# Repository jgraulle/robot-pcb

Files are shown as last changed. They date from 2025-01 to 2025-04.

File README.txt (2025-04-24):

Generate file for jlcpcb production:
- Run DRC check
- Generating Gerbers
   - File -> Fabrication Outputs -> Gerbers (.gbr)
   - Select the folder "build"
   - Layer selection, List of layers that should be selected:
      - F.Cu
      - B.Cu
      - F.Paste
      - B.Paste
      - F.Silkscreen
      - B.Silkscreen
      - F.Mask
      - B.Mask
      - Edge.Cuts - (contain the board outline/cutouts.)
   - Jump to General Options and check these:
      - Select Plot reference designators, otherwise designators will not appear on silkscreen layers
      - Select Plot footprint text
      - Select Check zone fills before plotting
      - Select Tent vias
      - Select Use Protel filename extensions, this is recommended as JLCPCB prefers Protel filename extensions
      - Select Subtract soldermask from silkscreen, this ensures no silkscreen on pads
   - Click the Plot button at the bottom of the window
- Generate Drill files
   - From previous window press the "Generate Drill files..." button
   - Check Use alternate drill mode for "Oval Holes Drill Mode"
   - Check Absolute for "Drill Origin"
   - Check Millimeters for "Drill Units"
   - Check Decimal format for "Zeros Format"
   - Click the Generate Drill File button, the drill files will be generated and stored in the output folder
- Generate Drill Map file
   - From previous window press the "Generate Map File" button and everything is going to be done automatically.
- Generate Bill of Materials
   - From Schematic Layout Editor. From the menu bar, click Tool -> Generate Bill of Materials
   - In edit tab, Only check in this order:
      - "Value" with label "Comment"
      - "Reference" with label "Designator"
      - "Package" with label "Footprint"
      - "LCSC" with label "LCSC part number"
   - In export tab:
       Set output file "build/robot-5A-bom.csv"
      - Clic on export
- Generate Pick and Place files
   - From the PCB editor, click on File -> Fabrication output -> Footprint position (.pos) file and export the file with the following settings:
      - CSV
      - mm
      - One file per side
      - Use drilling/placement origin
   - Run the scrip "jlcGenerate.sh"

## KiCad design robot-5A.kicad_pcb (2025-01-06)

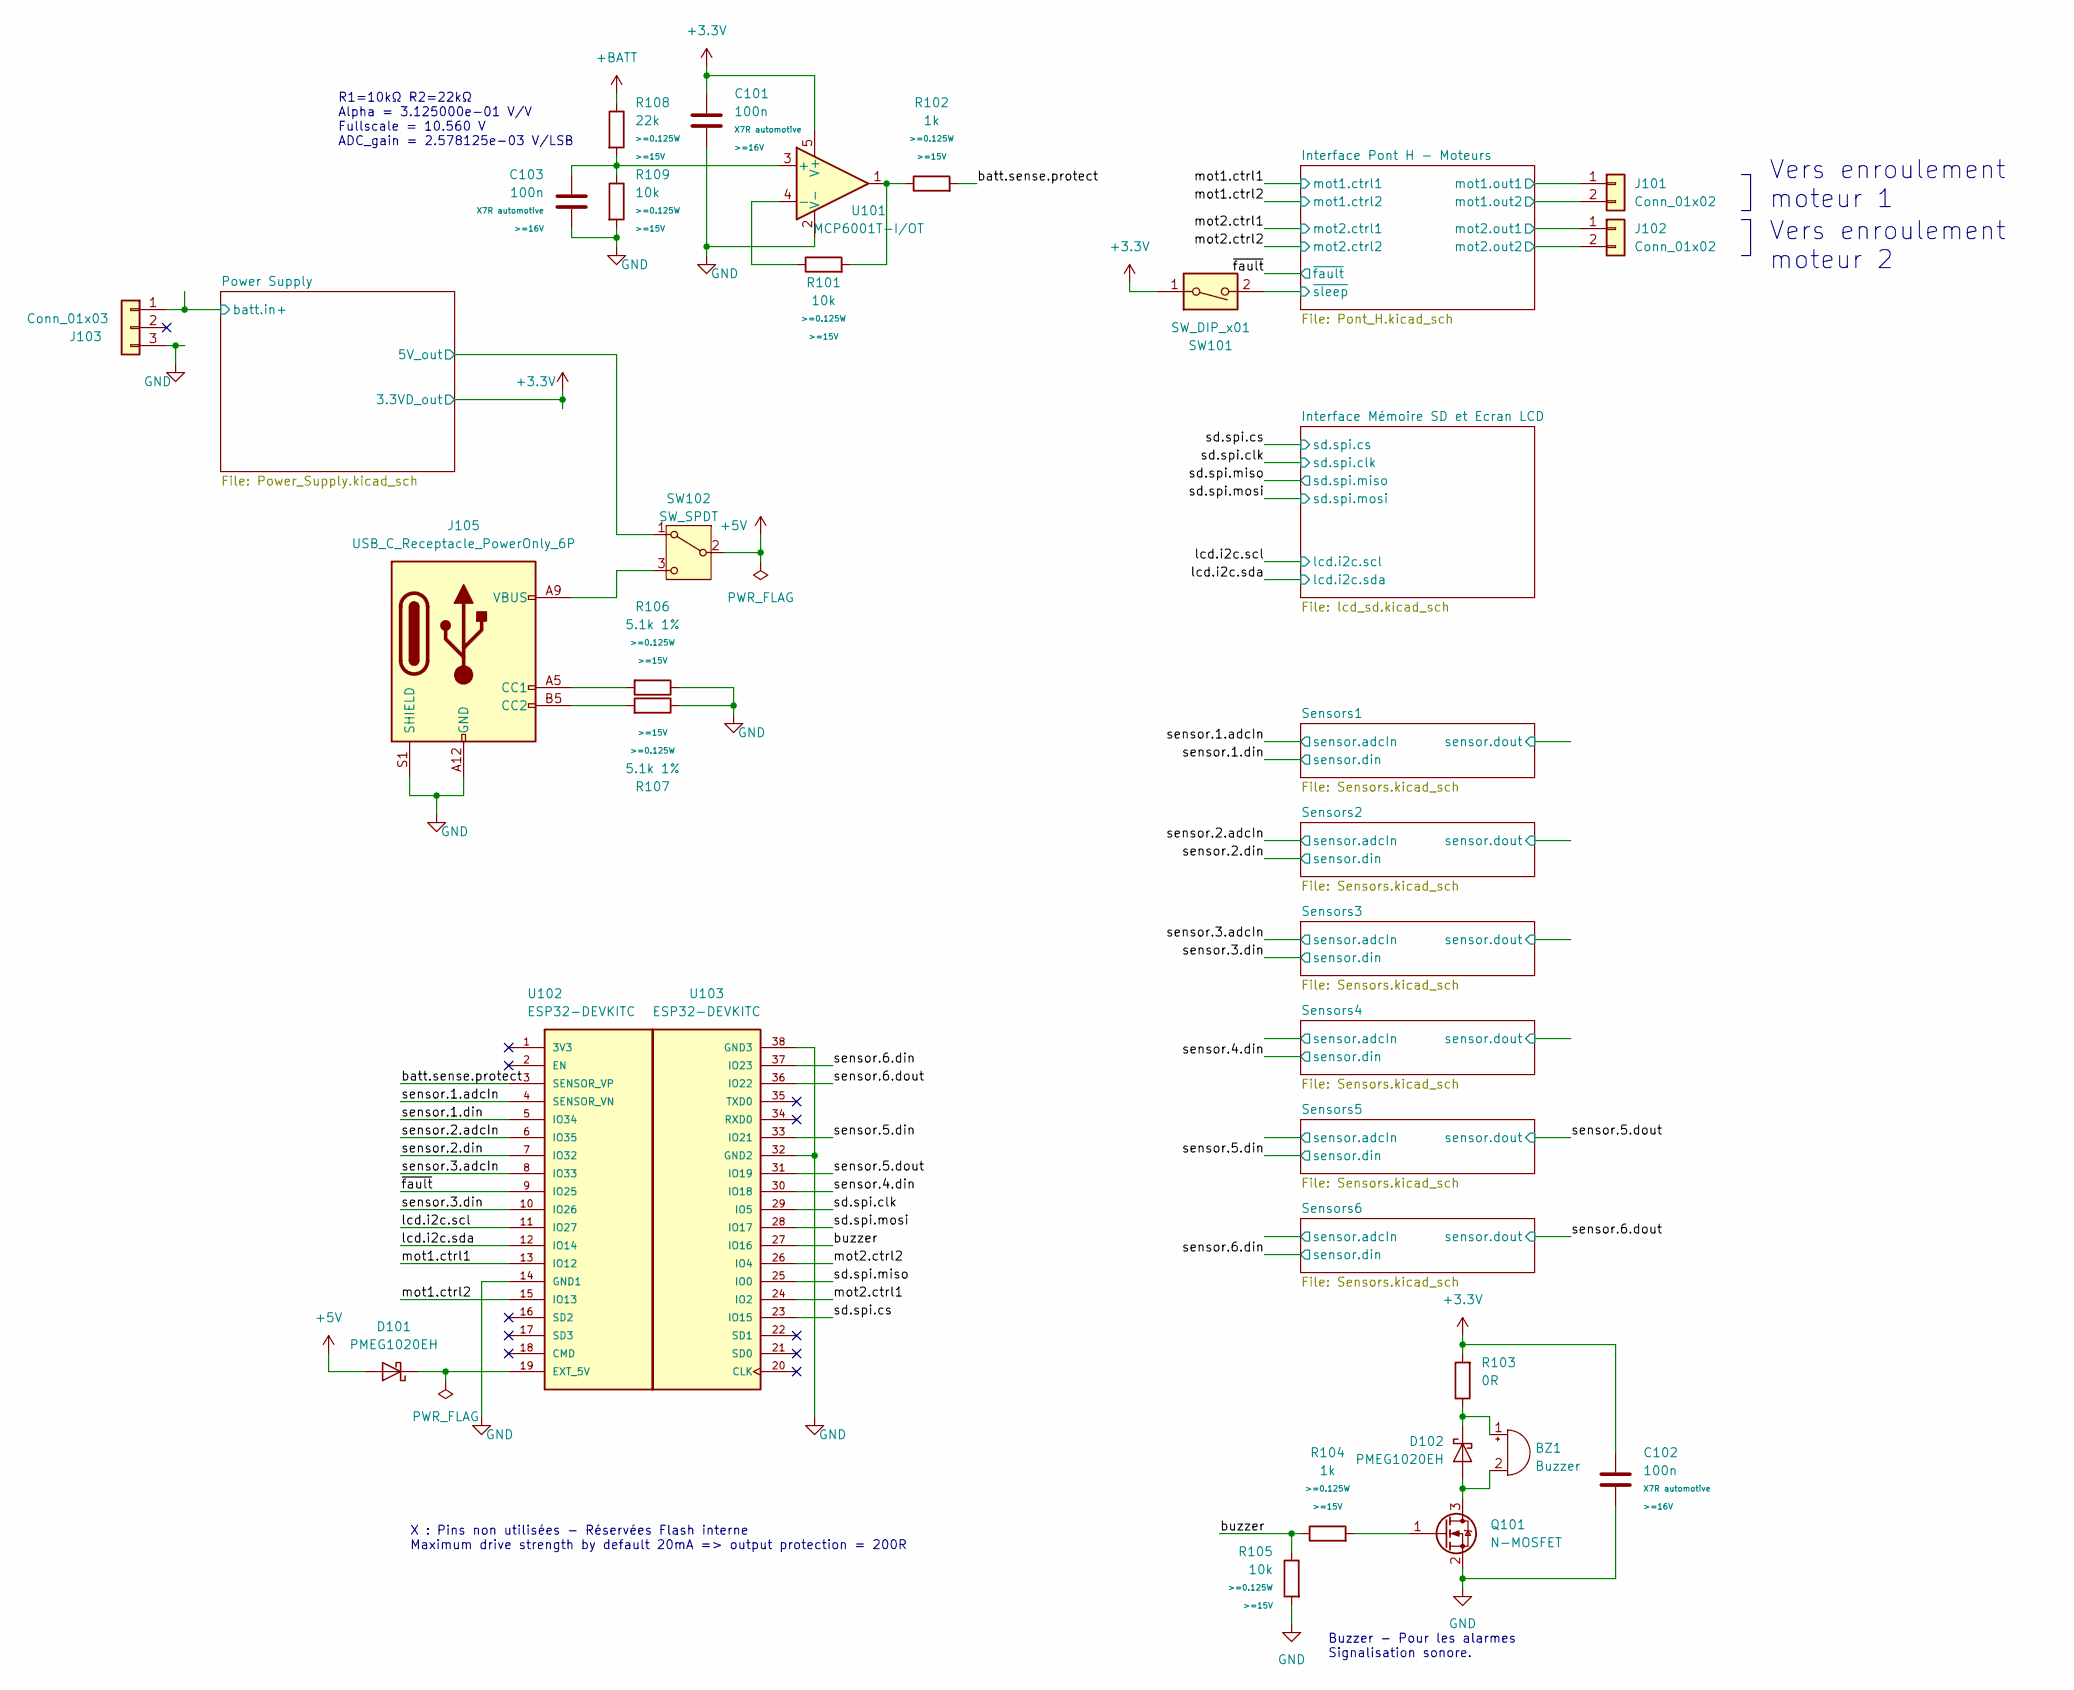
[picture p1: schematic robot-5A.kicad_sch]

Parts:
BZ1: Buzzer; MagneticBuzzer_PUI_AT-0927-TT-6-R; MPN QMB-09B-03; LCSC C96256
C101, C102, C103: 100n; C_0805_2012Metric; Tolerance <=10%; LCSC C28233
D101, D102: PMEG1020EH; D_SOD-123F; MPN PMEG1020EH; LCSC C552798
J101, J102: Conn_01x02; JST_XH_B2B-XH-AM_1x02_P2.50mm_Vertical; MPN XH 2.54; LCSC C158012
J103: Conn_01x03; JST_XH_B3B-XH-AM_1x03_P2.50mm_Vertical; MPN XH 2.54; LCSC C144394
J105: USB_C_Receptacle_PowerOnly_6P; USB_C_Receptacle_SHOU-HAN_TYPE-C-6P-LT-10.5; MPN TYPE-C 6P LT-10.5; LCSC C2681551
Q101: N-MOSFET; SOT-23; MPN AO3414; LCSC C48850
R101, R105, R109: 10k; R_0805_2012Metric; Tolerance <=1%; LCSC C17414
R102, R104: 1k; R_0805_2012Metric; Tolerance <=1%; LCSC C17513
R103: 0R; R_0805_2012Metric; LCSC C844192
R106, R107: 5.1k 1%; R_0805_2012Metric; Tolerance <=1%; LCSC C27834
R108: 22k; R_0805_2012Metric; Tolerance <=1%; LCSC C17560
SW101: SW_DIP_x01; SW_DIP_SPSTx01_Slide_9.78x4.72mm_W7.62mm_P2.54mm; LCSC C126888
SW102: SW_SPDT; SW_Slide_1P2T_SS-12F45; MPN SS-12F45-G040; LCSC C2876011
U101: MCP6001T-I/OT; SOT-23-5; LCSC C116490
U102, U103: ESP32-DEVKITC; MODULE_ESP32-DEVKITC; PARTREV N/A; LCSC C2932678

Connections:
+3.3V: C101.2, C102.2, R103.2, SW101.1, U101.5 (V+); also elsewhere on the board
+5V: D101.2 (A), SW102.2 (B); also elsewhere on the board
+BATT: R108.1; also elsewhere on the board
/Interface Pont H - Moteurs/mot1.out1: J101.1; also elsewhere on the board
/Interface Pont H - Moteurs/mot1.out2: J101.2; also elsewhere on the board
/Interface Pont H - Moteurs/mot2.out1: J102.1; also elsewhere on the board
/Interface Pont H - Moteurs/mot2.out2: J102.2; also elsewhere on the board
/Interface Pont H - Moteurs/~sleep: SW101.2; also elsewhere on the board
/Power Supply/5V_out: SW102.1 (A); also elsewhere on the board
/Power Supply/batt.in+: J103.1; also elsewhere on the board
/batt.sense.protect: R102.2, U102.3 (SENSOR_VP)
/buzzer: R104.1, R105.1, U103.27 (IO16)
/lcd.i2c.scl: U102.11 (IO27); also elsewhere on the board
/lcd.i2c.sda: U102.12 (IO14); also elsewhere on the board
/mot1.ctrl1: U102.13 (IO12); also elsewhere on the board
/mot1.ctrl2: U102.15 (IO13); also elsewhere on the board
/mot2.ctrl1: U103.24 (IO2); also elsewhere on the board
/mot2.ctrl2: U103.26 (IO4); also elsewhere on the board
/sd.spi.clk: U103.29 (IO5); also elsewhere on the board
/sd.spi.cs: U103.23 (IO15); also elsewhere on the board
/sd.spi.miso: U103.25 (IO0); also elsewhere on the board
/sd.spi.mosi: U103.28 (IO17); also elsewhere on the board
/sensor.1.adcIn: U102.4 (SENSOR_VN); also elsewhere on the board
/sensor.1.din: U102.5 (IO34); also elsewhere on the board
/sensor.2.adcIn: U102.6 (IO35); also elsewhere on the board
/sensor.2.din: U102.7 (IO32); also elsewhere on the board
/sensor.3.adcIn: U102.8 (IO33); also elsewhere on the board
/sensor.3.din: U102.10 (IO26); also elsewhere on the board
/sensor.4.din: U103.30 (IO18); also elsewhere on the board
/sensor.5.din: U103.33 (IO21); also elsewhere on the board
/sensor.5.dout: U103.31 (IO19); also elsewhere on the board
/sensor.6.din: U103.37 (IO23); also elsewhere on the board
/sensor.6.dout: U103.36 (IO22); also elsewhere on the board
/~fault: U102.9 (IO25); also elsewhere on the board
GND: C101.1, C102.1, C103.2, J103.3, J105.A12 (GND), J105.B12 (GND), J105.S1 (SHIELD), Q101.2 (S), R105.2, R106.1, R107.1, R109.2, U101.2 (V-), U102.14 (GND1), U103.32 (GND2), U103.38 (GND3); also elsewhere on the board
unnamed 48: D102.2 (A), Q101.3 (D); also elsewhere on the board
unnamed 49: D102.1 (K), R103.1; also elsewhere on the board
unnamed: D101.1 (K), U102.19 (EXT_5V)
unnamed: J105.A5 (CC1), R106.2
unnamed: J105.B5 (CC2), R107.2
unnamed: Q101.1 (G), R104.2
unnamed: R101.2, R102.1, U101.1
unnamed: J105.A9 (VBUS), J105.B9 (VBUS), SW102.3 (C)
unnamed: C103.1, R108.2, R109.1, U101.3 (+)
unnamed: R101.1, U101.4 (-)

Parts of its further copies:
BZ101: Buzzer; MagneticBuzzer_PUI_AT-0927-TT-6-R; MPN QMB-09B-03; LCSC C96256

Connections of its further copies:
unnamed 48: BZ101.2 (+); also elsewhere on the board
unnamed 49: BZ101.1 (-); also elsewhere on the board

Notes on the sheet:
Vers enroulement moteur 1
R1=10kΩ R2=22kΩ Alpha = 3.125000e-01 V/V Fullscale = 10.560 V ADC_gain = 2.578125e-03 V/LSB
X : Pins non utilisées - Réservées Flash interne Maximum drive strength by default 20mA => output protection = 200R
Vers enroulement moteur 2
Buzzer - Pour les alarmes Signalisation sonore.

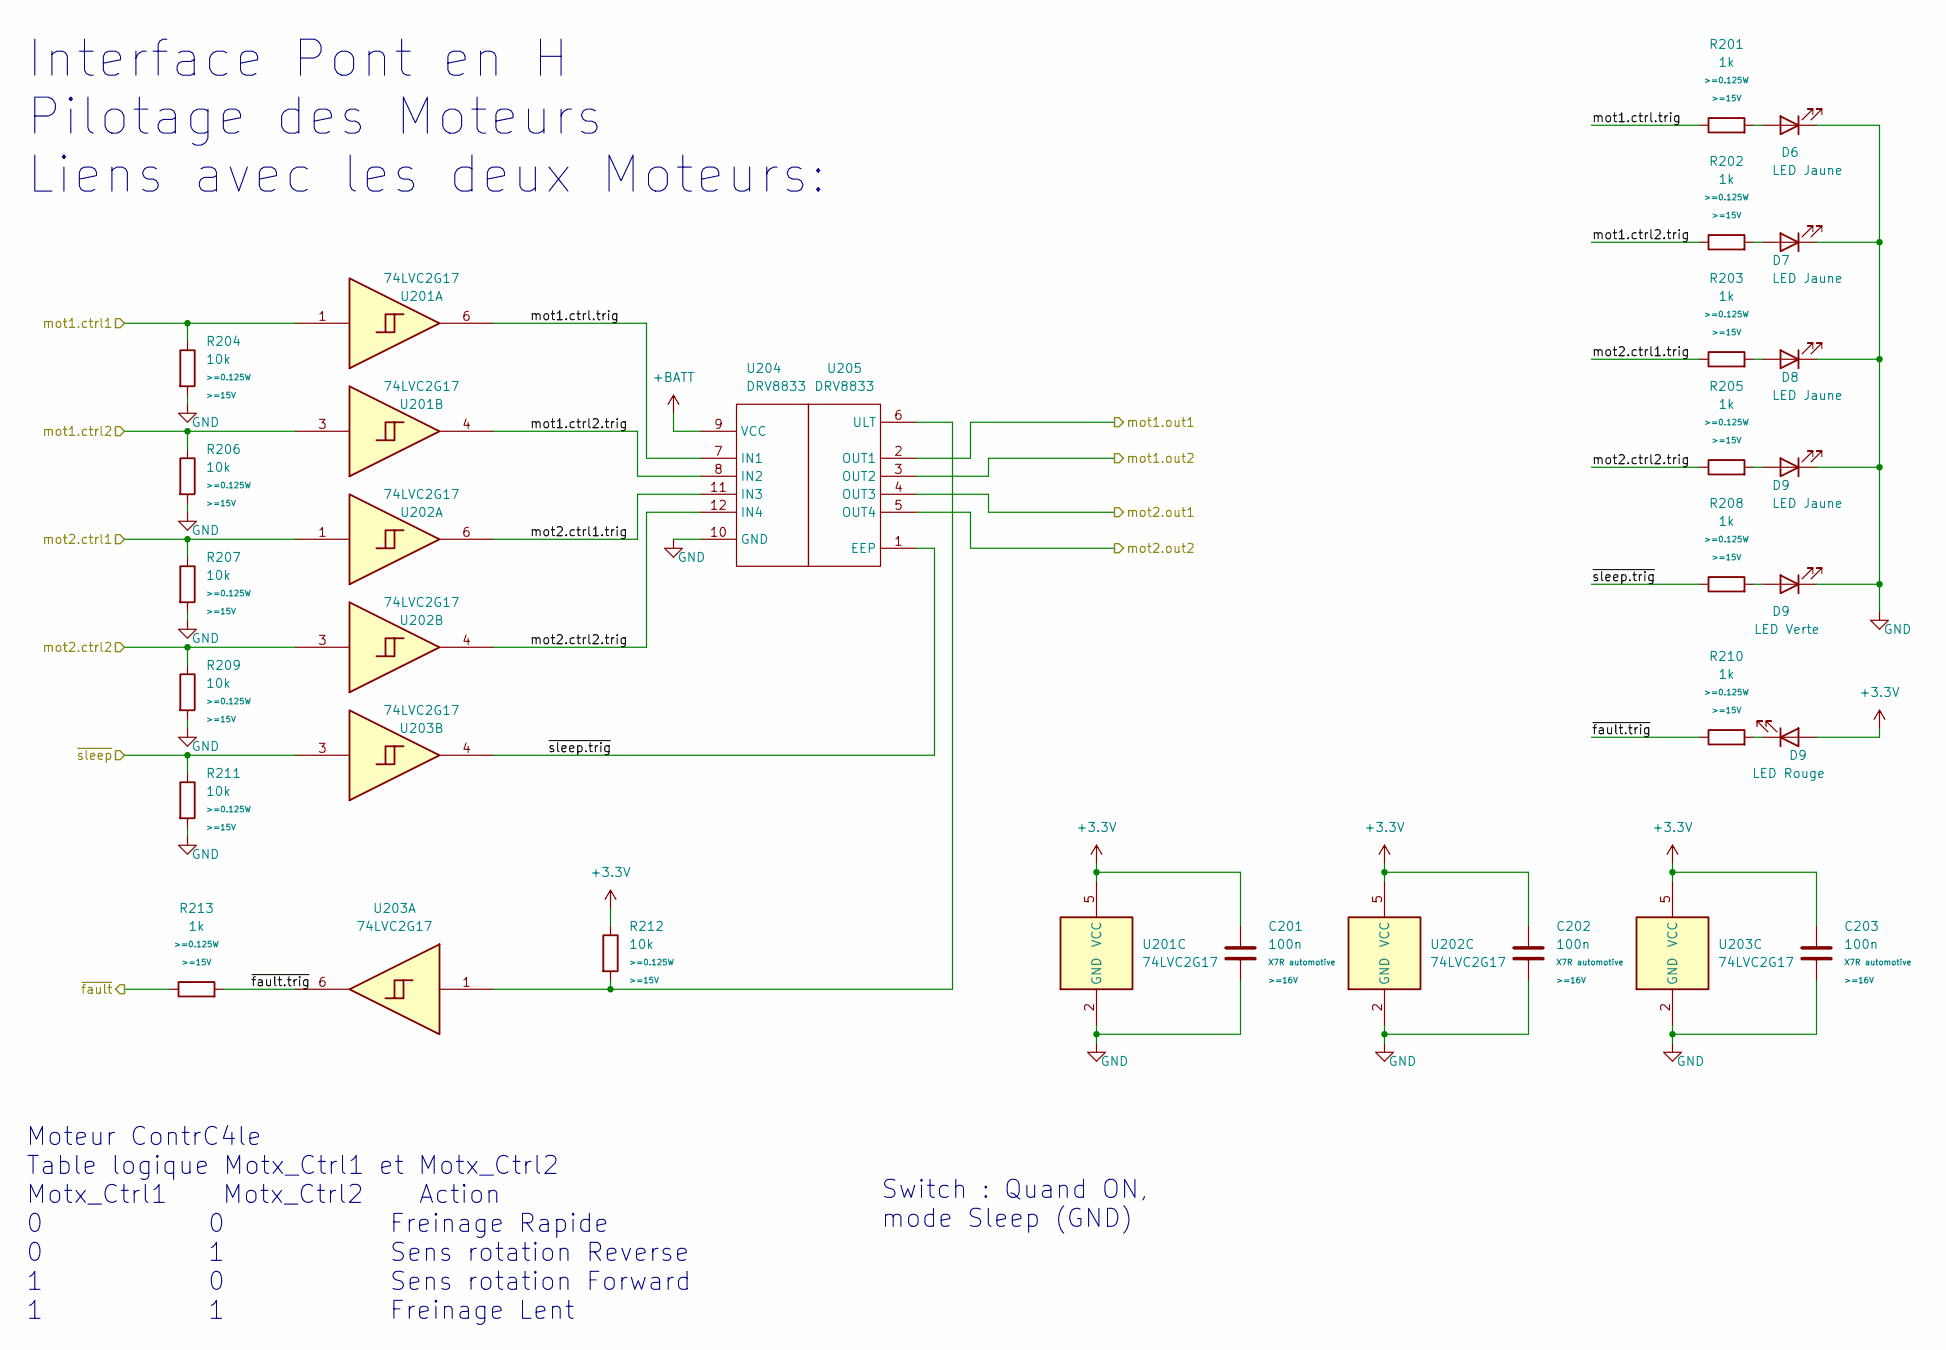
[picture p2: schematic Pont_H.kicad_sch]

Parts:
C201, C202, C203: 100n; C_0805_2012Metric; Tolerance <=10%; LCSC C28233
D6, D7, D8: LED Jaune; LED_0805_2012Metric; MPN KP-2012SYCK; LCSC C2296
D9: LED Rouge; LED_0805_2012Metric; MPN KP-2012SURCK; LCSC C84256
R201, R202, R203, R205, R208, R210, R213: 1k; R_0805_2012Metric; Tolerance <=1%; LCSC C17513
R204, R206, R207, R209, R211, R212: 10k; R_0805_2012Metric; Tolerance <=1%; LCSC C17414
U201, U202, U203: 74LVC2G17; SOT-23-6; MPN SN74LVC2G17DBVR; LCSC C10429
U204, U205: DRV8833; DVR8833_EVM; LCSC C40877

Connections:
+3.3V: C201.1, C202.1, C203.1, R212.1, U201.5 (VCC), U202.5 (VCC), U203.5 (VCC); also elsewhere on the board
+BATT: U204.9 (VCC); also elsewhere on the board
/Interface Pont H - Moteurs/mot1.ctrl2.trig: R202.1, U201.4, U204.8 (IN2)
/Interface Pont H - Moteurs/mot1.ctrl.trig: R201.1, U201.6, U204.7 (IN1)
/Interface Pont H - Moteurs/mot1.out1: U205.2 (OUT1); also elsewhere on the board
/Interface Pont H - Moteurs/mot1.out2: U205.3 (OUT2); also elsewhere on the board
/Interface Pont H - Moteurs/mot2.ctrl1.trig: R203.1, U202.6, U204.11 (IN3)
/Interface Pont H - Moteurs/mot2.ctrl2.trig: R205.1, U202.4, U204.12 (IN4)
/Interface Pont H - Moteurs/mot2.out1: U205.4 (OUT3); also elsewhere on the board
/Interface Pont H - Moteurs/mot2.out2: U205.5 (OUT4); also elsewhere on the board
/Interface Pont H - Moteurs/~fault.trig: R210.1, R213.2, U203.6
/Interface Pont H - Moteurs/~sleep.trig: R208.1, U203.4, U205.1 (EEP)
/Interface Pont H - Moteurs/~sleep: R211.1, U203.3; also elsewhere on the board
/mot1.ctrl1: R204.1, U201.1; also elsewhere on the board
/mot1.ctrl2: R206.1, U201.3; also elsewhere on the board
/mot2.ctrl1: R207.1, U202.1; also elsewhere on the board
/mot2.ctrl2: R209.1, U202.3; also elsewhere on the board
/~fault: R213.1; also elsewhere on the board
GND: C201.2, C202.2, C203.2, R204.2, R206.2, R207.2, R209.2, R211.2, U201.2 (GND), U202.2 (GND), U203.2 (GND), U204.10 (GND); also elsewhere on the board
unnamed 53: R201.2; also elsewhere on the board
unnamed 54: R202.2; also elsewhere on the board
unnamed 55: R203.2; also elsewhere on the board
unnamed 56: R205.2; also elsewhere on the board
unnamed 57: R208.2; also elsewhere on the board
unnamed 58: R210.2; also elsewhere on the board
unnamed: R212.2, U203.1, U205.6 (ULT)

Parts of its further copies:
D201, D202, D203: LED Jaune; LED_0805_2012Metric; MPN KP-2012SYCK; LCSC C2296
D206: LED Rouge; LED_0805_2012Metric; MPN KP-2012SURCK; LCSC C84256

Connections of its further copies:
+3.3V: D206.2 (A); also elsewhere on the board
GND: D201.1 (K), D202.1 (K), D203.1 (K); also elsewhere on the board
unnamed 53: D201.2 (A); also elsewhere on the board
unnamed 54: D202.2 (A); also elsewhere on the board
unnamed 55: D203.2 (A); also elsewhere on the board
unnamed 58: D206.1 (K); also elsewhere on the board

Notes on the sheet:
Moteur ContrC4le Table logique Motx_Ctrl1 et Motx_Ctrl2 Motx_Ctrl1 Motx_Ctrl2 Action 0 0 Freinage Rapide 0 1 Sens rotation Reverse 1 0 Sens rotation Forward 1 1 Freinage Lent
Switch : Quand ON, mode Sleep (GND)
Interface Pont en H Pilotage des Moteurs Liens avec les deux Moteurs:

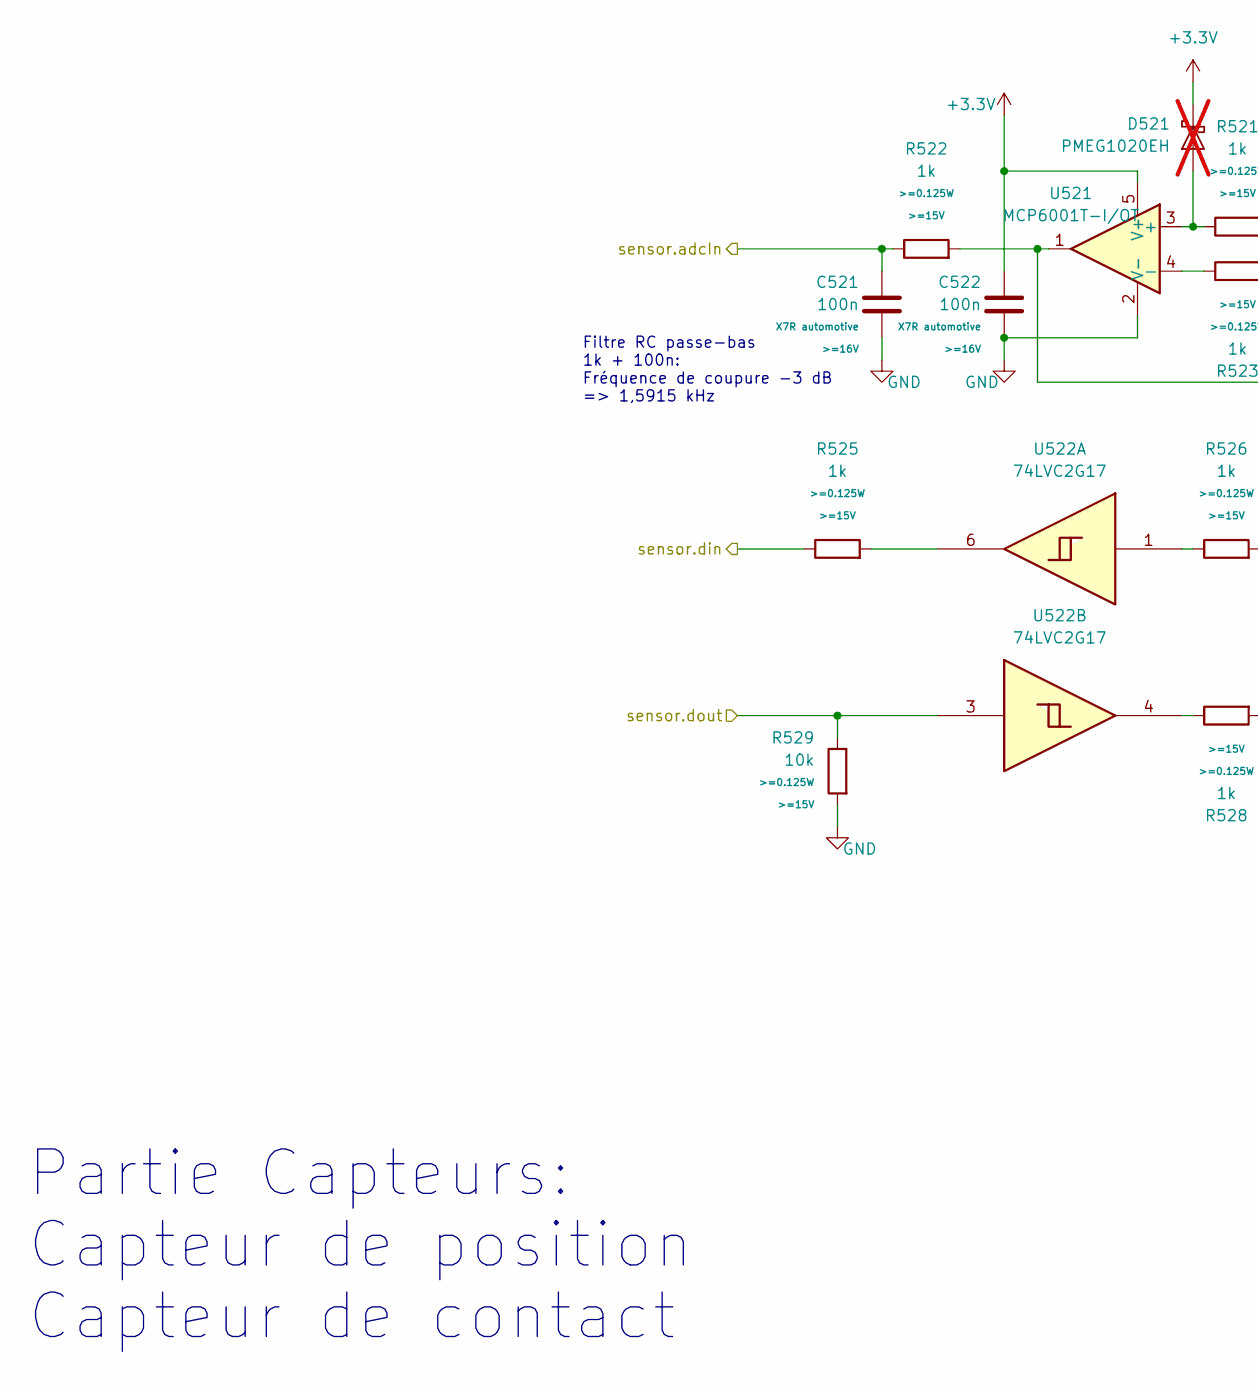
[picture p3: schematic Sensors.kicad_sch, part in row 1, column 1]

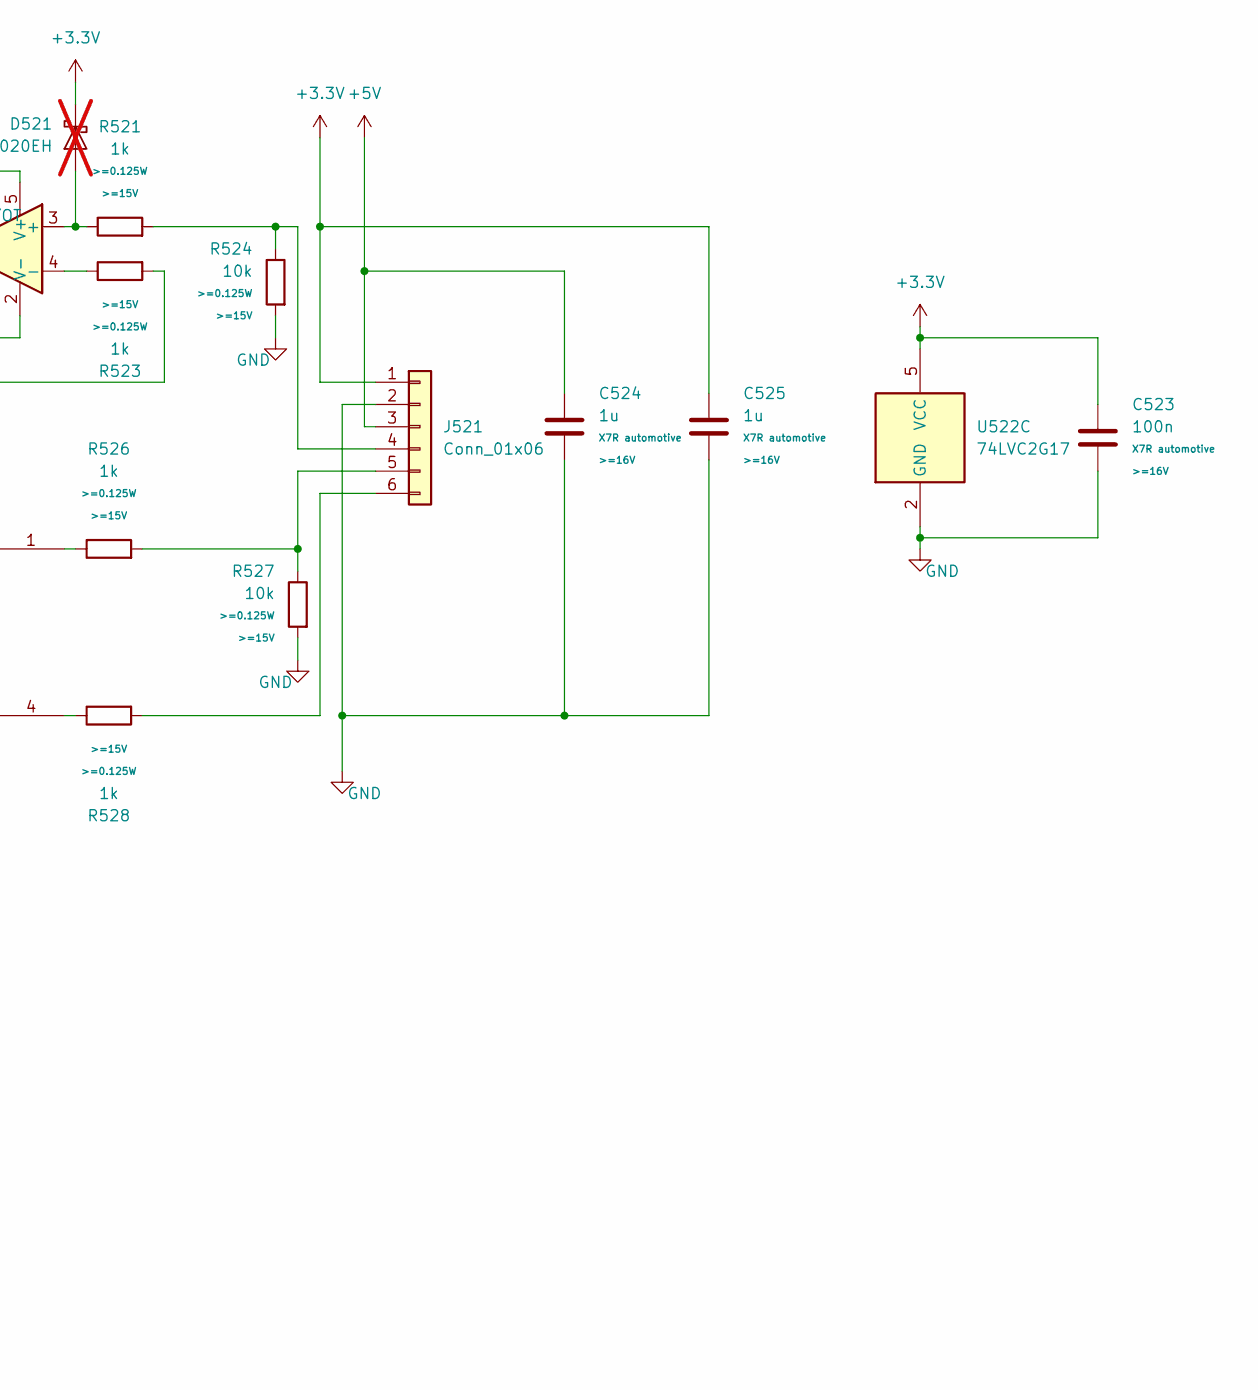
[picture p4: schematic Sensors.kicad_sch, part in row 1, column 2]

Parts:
C521, C522, C523: 100n; C_0805_2012Metric; Tolerance <=10%; LCSC C28233
C524, C525: 1u; C_0805_2012Metric; Tolerance <=10%; LCSC C28323
D521: PMEG1020EH; D_SOD-123F; MPN PMEG1020EH; LCSC C552798; not fitted
J521: Conn_01x06; JST_XH_B6B-XH-AM_1x06_P2.50mm_Vertical; MPN XH 2.54; LCSC C144397
R521, R522, R523, R525, R526, R528: 1k; R_0805_2012Metric; Tolerance <=1%; LCSC C17513
R524, R527, R529: 10k; R_0805_2012Metric; Tolerance <=1%; LCSC C17414
U521: MCP6001T-I/OT; SOT-23-5; LCSC C116490
U522: 74LVC2G17; SOT-23-6; MPN SN74LVC2G17DBVR; LCSC C10429

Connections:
+3.3V: C522.2, C523.1, C525.1, D521.1 (K), J521.1, U521.5 (V+), U522.5 (VCC); also elsewhere on the board
+5V: C524.1, J521.3; also elsewhere on the board
/Sensors2/sensor.dout: R529.1, U522.3
/sensor.2.adcIn: C521.2, R522.1; also elsewhere on the board
/sensor.2.din: R525.1; also elsewhere on the board
GND: C521.1, C522.1, C523.2, C524.2, C525.2, J521.2, R524.2, R527.2, R529.2, U521.2 (V-), U522.2 (GND); also elsewhere on the board
unnamed: D521.2 (A), R521.1, U521.3 (+)
unnamed: J521.4, R521.2, R524.1
unnamed: J521.5, R526.2, R527.1
unnamed: J521.6, R528.2
unnamed: R522.2, R523.2, U521.1
unnamed: R525.2, U522.6
unnamed: R526.1, U522.1
unnamed: R528.1, U522.4
unnamed: R523.1, U521.4 (-)

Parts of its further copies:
C511, C512, C513, C531, C532, C533, C541, C542, C543, C551, C552, C553, C561, C562, C563: 100n; C_0805_2012Metric; Tolerance <=10%; LCSC C28233
C514, C515, C534, C535, C544, C545, C554, C555, C564, C565: 1u; C_0805_2012Metric; Tolerance <=10%; LCSC C28323
D511, D531, D541, D551, D561: PMEG1020EH; D_SOD-123F; MPN PMEG1020EH; LCSC C552798; not fitted
J511, J531, J541, J551, J561: Conn_01x06; JST_XH_B6B-XH-AM_1x06_P2.50mm_Vertical; MPN XH 2.54; LCSC C144397
R511, R512, R513, R515, R516, R518, R531, R532, R533, R535, R536, R538, R541, R542, R543, R545, R546, R548, R551, R552, R553, R555, R556, R558, R561, R562, R563, R565, R566, R568: 1k; R_0805_2012Metric; Tolerance <=1%; LCSC C17513
R514, R517, R519, R534, R537, R539, R544, R547, R549, R554, R557, R559, R564, R567, R569: 10k; R_0805_2012Metric; Tolerance <=1%; LCSC C17414
U511, U531, U541, U551, U561: MCP6001T-I/OT; SOT-23-5; LCSC C116490
U512, U532, U542, U552, U562: 74LVC2G17; SOT-23-6; MPN SN74LVC2G17DBVR; LCSC C10429

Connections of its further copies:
+3.3V: C512.2, C513.1, C515.1, C532.2, C533.1, C535.1, C542.2, C543.1, C545.1, C552.2, C553.1, C555.1, C562.2, C563.1, C565.1, D511.1 (K), D531.1 (K), D541.1 (K), D551.1 (K), D561.1 (K), J511.1, J531.1, J541.1, J551.1, J561.1, U511.5 (V+), U512.5 (VCC), U531.5 (V+), U532.5 (VCC), U541.5 (V+), U542.5 (VCC), U551.5 (V+), U552.5 (VCC), U561.5 (V+), U562.5 (VCC); also elsewhere on the board
+5V: C514.1, C534.1, C544.1, C554.1, C564.1, J511.3, J531.3, J541.3, J551.3, J561.3; also elsewhere on the board
/Sensors1/sensor.dout: R519.1, U512.3
/Sensors3/sensor.dout: R539.1, U532.3
/Sensors4/sensor.adcIn: C541.2, R542.1
/Sensors4/sensor.dout: R549.1, U542.3
/Sensors5/sensor.adcIn: C551.2, R552.1
/Sensors6/sensor.adcIn: C561.2, R562.1
/sensor.1.adcIn: C511.2, R512.1; also elsewhere on the board
/sensor.1.din: R515.1; also elsewhere on the board
/sensor.3.adcIn: C531.2, R532.1; also elsewhere on the board
/sensor.3.din: R535.1; also elsewhere on the board
/sensor.4.din: R545.1; also elsewhere on the board
/sensor.5.din: R555.1; also elsewhere on the board
/sensor.5.dout: R559.1, U552.3; also elsewhere on the board
/sensor.6.din: R565.1; also elsewhere on the board
/sensor.6.dout: R569.1, U562.3; also elsewhere on the board
GND: C511.1, C512.1, C513.2, C514.2, C515.2, C531.1, C532.1, C533.2, C534.2, C535.2, C541.1, C542.1, C543.2, C544.2, C545.2, C551.1, C552.1, C553.2, C554.2, C555.2, C561.1, C562.1, C563.2, C564.2, C565.2, J511.2, J531.2, J541.2, J551.2, J561.2, R514.2, R517.2, R519.2, R534.2, R537.2, R539.2, R544.2, R547.2, R549.2, R554.2, R557.2, R559.2, R564.2, R567.2, R569.2, U511.2 (V-), U512.2 (GND), U531.2 (V-), U532.2 (GND), U541.2 (V-), U542.2 (GND), U551.2 (V-), U552.2 (GND), U561.2 (V-), U562.2 (GND); also elsewhere on the board
unnamed: D511.2 (A), R511.1, U511.3 (+)
unnamed: D531.2 (A), R531.1, U531.3 (+)
unnamed: D541.2 (A), R541.1, U541.3 (+)
unnamed: D551.2 (A), R551.1, U551.3 (+)
unnamed: D561.2 (A), R561.1, U561.3 (+)
unnamed: J511.4, R511.2, R514.1
unnamed: J511.5, R516.2, R517.1
unnamed: J511.6, R518.2
unnamed: J531.4, R531.2, R534.1
unnamed: J531.5, R536.2, R537.1
unnamed: J531.6, R538.2
unnamed: J541.4, R541.2, R544.1
unnamed: J541.5, R546.2, R547.1
unnamed: J541.6, R548.2
unnamed: J551.4, R551.2, R554.1
unnamed: J551.5, R556.2, R557.1
unnamed: J551.6, R558.2
unnamed: J561.4, R561.2, R564.1
unnamed: J561.5, R566.2, R567.1
unnamed: J561.6, R568.2
unnamed: R512.2, R513.2, U511.1
unnamed: R515.2, U512.6
unnamed: R516.1, U512.1
unnamed: R518.1, U512.4
unnamed: R532.2, R533.2, U531.1
unnamed: R535.2, U532.6
unnamed: R536.1, U532.1
unnamed: R538.1, U532.4
unnamed: R542.2, R543.2, U541.1
unnamed: R545.2, U542.6
unnamed: R546.1, U542.1
unnamed: R548.1, U542.4
unnamed: R552.2, R553.2, U551.1
unnamed: R555.2, U552.6
unnamed: R556.1, U552.1
unnamed: R558.1, U552.4
unnamed: R562.2, R563.2, U561.1
unnamed: R565.2, U562.6
unnamed: R566.1, U562.1
unnamed: R568.1, U562.4
unnamed: R513.1, U511.4 (-)
unnamed: R533.1, U531.4 (-)
unnamed: R543.1, U541.4 (-)
unnamed: R553.1, U551.4 (-)
unnamed: R563.1, U561.4 (-)

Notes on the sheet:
Filtre RC passe-bas 1k + 100n: Fréquence de coupure -3 dB => 1,5915 kHz
Partie Capteurs: Capteur de position Capteur de contact

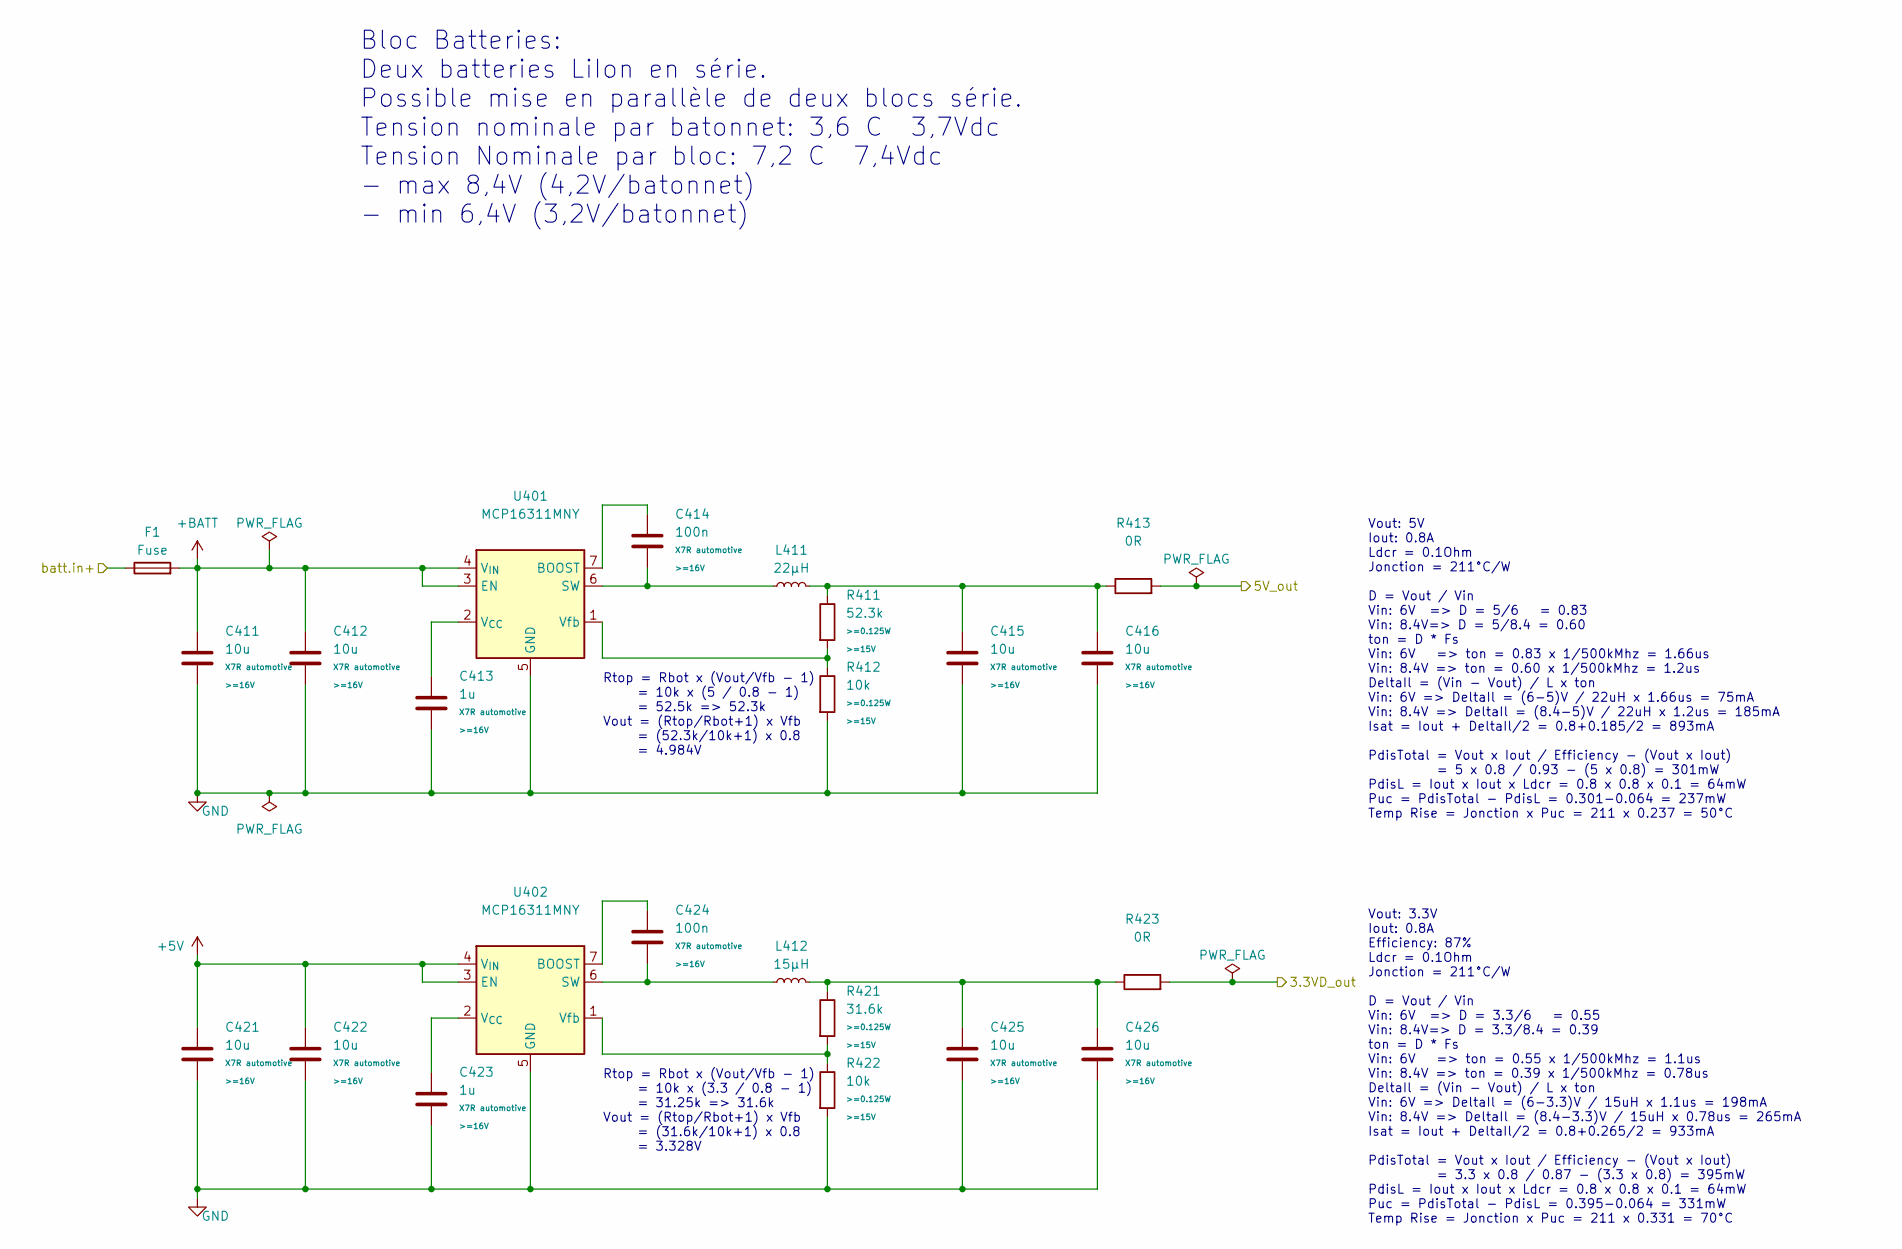
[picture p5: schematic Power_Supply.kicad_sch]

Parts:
C411, C412, C415, C416, C421, C422, C425, C426: 10u; C_1210_3225Metric; Tolerance <=10%; LCSC C39232
C413, C423: 1u; C_0805_2012Metric; Tolerance <=10%; LCSC C28323
C414, C424: 100n; C_0805_2012Metric; Tolerance <=10%; LCSC C28233
F1: Fuse; Fuse_1206_3216Metric; LCSC C182310
L411: 22µH; L_KOHERelec_MDA-7050; LCSC C2847545
L412: 15µH; L_KOHERelec_MDA-7050; LCSC C2847544
R411: 52.3k; R_0805_2012Metric; Tolerance <=1%; LCSC C2078257
R412, R422: 10k; R_0805_2012Metric; Tolerance <=1%; LCSC C17414
R413, R423: 0R; R_0805_2012Metric; LCSC C844192
R421: 31.6k; R_0805_2012Metric; Tolerance <=1%; LCSC C170879
U401, U402: MCP16311MNY; TDFN-8-1EP_3x2mm_P0.5mm_EP1.60x1.50mm; MPN MCP16311T-E/MNY; LCSC C510882

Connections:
+3.3V: R423.2; also elsewhere on the board
+5V: C421.2, C422.2, U402.3 (EN), U402.4 (Vin); also elsewhere on the board
+BATT: C411.2, C412.2, U401.3 (EN), U401.4 (Vin); also elsewhere on the board
/Power Supply/5V_out: R413.2; also elsewhere on the board
GND: C411.1, C412.1, C413.2, C415.1, C416.1, C421.1, C422.1, C423.2, C425.1, C426.1, R412.2, R422.2, U401.5 (PGND), U401.8 (AGND), U401.9 (PAD), U402.5 (PGND), U402.8 (AGND), U402.9 (PAD); also elsewhere on the board
unnamed: C415.2, C416.2, L411.2, R411.1, R413.1
unnamed: C425.2, C426.2, L412.2, R421.1, R423.1
unnamed: C414.1, U401.7 (BOOST)
unnamed: C414.2, L411.1, U401.6 (SW)
unnamed: C413.1, U401.2 (Vcc)
unnamed: R411.2, R412.1, U401.1 (Vfb)
unnamed: C424.1, U402.7 (BOOST)
unnamed: C424.2, L412.1, U402.6 (SW)
unnamed: C423.1, U402.2 (Vcc)
unnamed: R421.2, R422.1, U402.1 (Vfb)

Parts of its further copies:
F401: Fuse; Fuse_1206_3216Metric; LCSC C182310

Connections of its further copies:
+BATT: F401.2; also elsewhere on the board
/Power Supply/batt.in+: F401.1; also elsewhere on the board

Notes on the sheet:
Bloc Batteries: Deux batteries LiIon en série. Possible mise en parallèle de deux blocs série. Tension nominale par batonnet: 3,6 C 3,7Vdc Tension Nominale par bloc: 7,2 C 7,4Vdc - max 8,4V (4,2V/batonnet) - min 6,4V (3,2V/batonnet)
Rtop = Rbot x (Vout/Vfb - 1) = 10k x (3.3 / 0.8 - 1) = 31.25k => 31.6k Vout = (Rtop/Rbot+1) x Vfb = (31.6k/10k+1) x 0.8 = 3.328V
Vout: 3.3V Iout: 0.8A Efficiency: 87% Ldcr = 0.1Ohm Jonction = 211°C/W D = Vout / Vin Vin: 6V => D = 3.3/6 = 0.55 Vin: 8.4V=> D = 3.3/8.4 = 0.39 ton = D * Fs Vin: 6V => ton = 0.55 x 1/500kMhz = 1.1us Vin: 8.4V => ton = 0.39 x 1/500kMhz = 0.78us DeltaIl = (Vin - Vout) / L x ton Vin: 6V => DeltaIl = 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
Vout: 5V Iout: 0.8A Ldcr = 0.1Ohm Jonction = 211°C/W D = Vout / Vin Vin: 6V => D = 5/6 = 0.83 Vin: 8.4V=> D = 5/8.4 = 0.60 ton = D * Fs Vin: 6V => ton = 0.83 x 1/500kMhz = 1.66us Vin: 8.4V => ton = 0.60 x 1/500kMhz = 1.2us DeltaIl = (Vin - Vout) / L x ton Vin: 6V => DeltaIl = (6-5)V / 22uH x 1.66us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
Rtop = Rbot x (Vout/Vfb - 1) = 10k x (5 / 0.8 - 1) = 52.5k => 52.3k Vout = (Rtop/Rbot+1) x Vfb = (52.3k/10k+1) x 0.8 = 4.984V

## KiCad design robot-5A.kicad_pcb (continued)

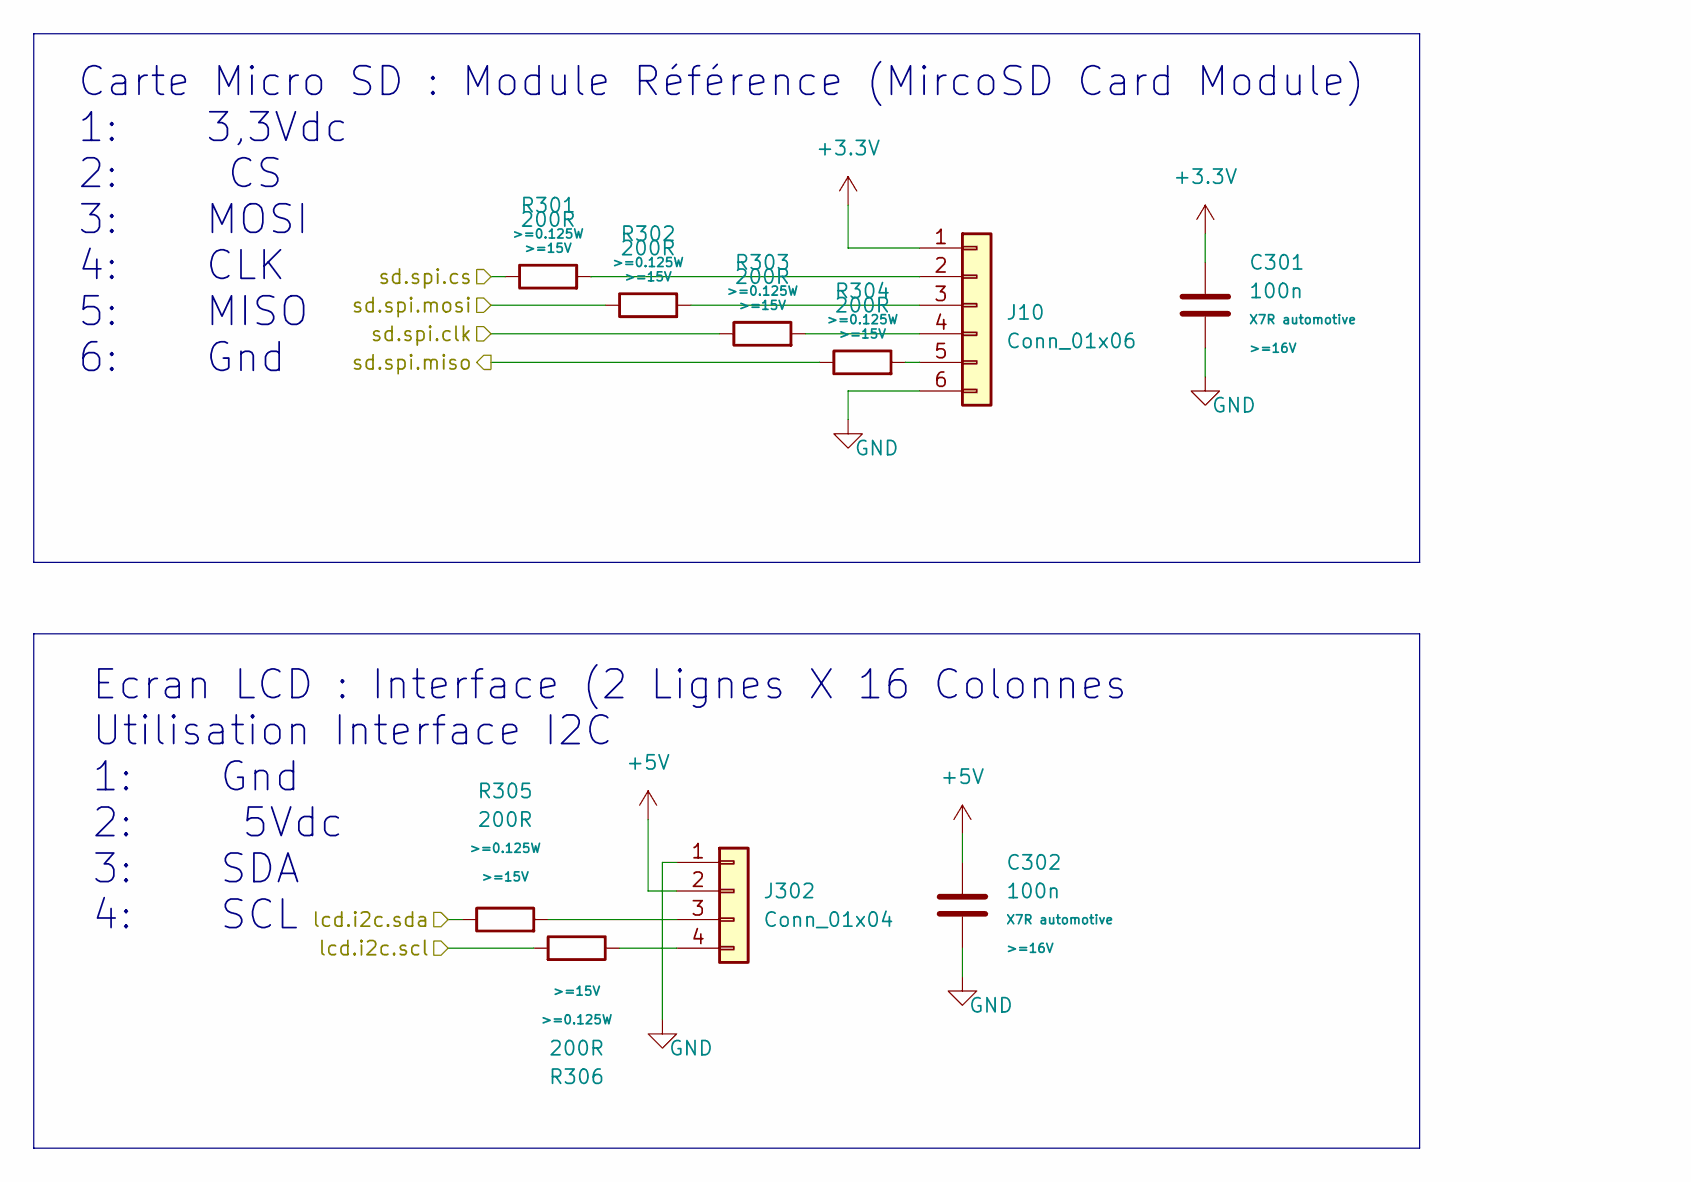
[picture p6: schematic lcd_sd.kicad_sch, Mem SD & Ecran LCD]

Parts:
C301, C302: 100n; C_0805_2012Metric; Tolerance <=10%; LCSC C28233
J10: Conn_01x06; PinSocket_1x06_P2.54mm_Vertical; LCSC C40877
J302: Conn_01x04; PinHeader_1x04_P2.54mm_Vertical; LCSC C6332197
R301, R302, R303, R304, R305, R306: 200R; R_0805_2012Metric; Tolerance <=1%; LCSC C17540

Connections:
+3.3V: C301.1; also elsewhere on the board
+5V: C302.1, J302.2; also elsewhere on the board
/lcd.i2c.scl: R306.2; also elsewhere on the board
/lcd.i2c.sda: R305.1; also elsewhere on the board
/sd.spi.clk: R303.1; also elsewhere on the board
/sd.spi.cs: R301.1; also elsewhere on the board
/sd.spi.miso: R304.1; also elsewhere on the board
/sd.spi.mosi: R302.1; also elsewhere on the board
GND: C301.2, C302.2, J302.1; also elsewhere on the board
unnamed 67: R301.2; also elsewhere on the board
unnamed 68: R302.2; also elsewhere on the board
unnamed 69: R303.2; also elsewhere on the board
unnamed 70: R304.2; also elsewhere on the board
unnamed: J302.3, R305.2
unnamed: J302.4, R306.1

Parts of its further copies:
J301: Conn_01x06; PinSocket_1x06_P2.54mm_Vertical; LCSC C40877

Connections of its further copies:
+3.3V: J301.1; also elsewhere on the board
GND: J301.6; also elsewhere on the board
unnamed 67: J301.2; also elsewhere on the board
unnamed 68: J301.3; also elsewhere on the board
unnamed 69: J301.4; also elsewhere on the board
unnamed 70: J301.5; also elsewhere on the board

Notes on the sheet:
Ecran LCD : Interface (2 Lignes X 16 Colonnes Utilisation Interface I2C 1: Gnd 2: 5Vdc 3: SDA 4: SCL
Carte Micro SD : Module Référence (MircoSD Card Module) 1: 3,3Vdc 2: CS 3: MOSI 4: CLK 5: MISO 6: Gnd

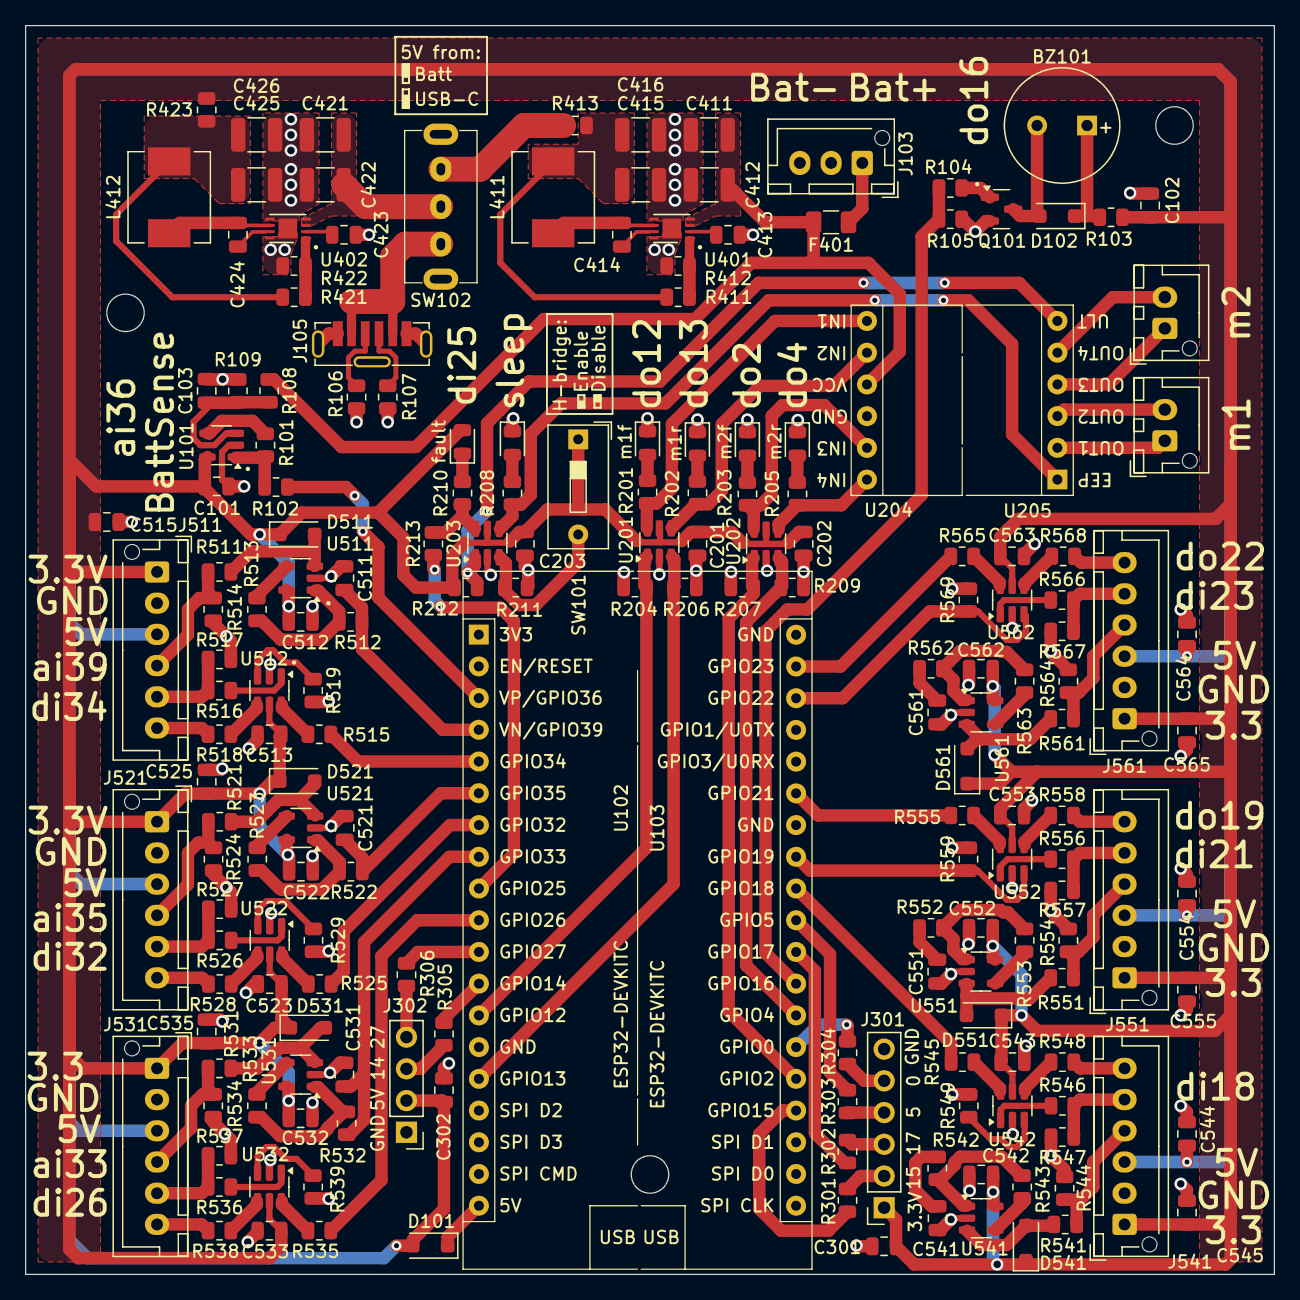
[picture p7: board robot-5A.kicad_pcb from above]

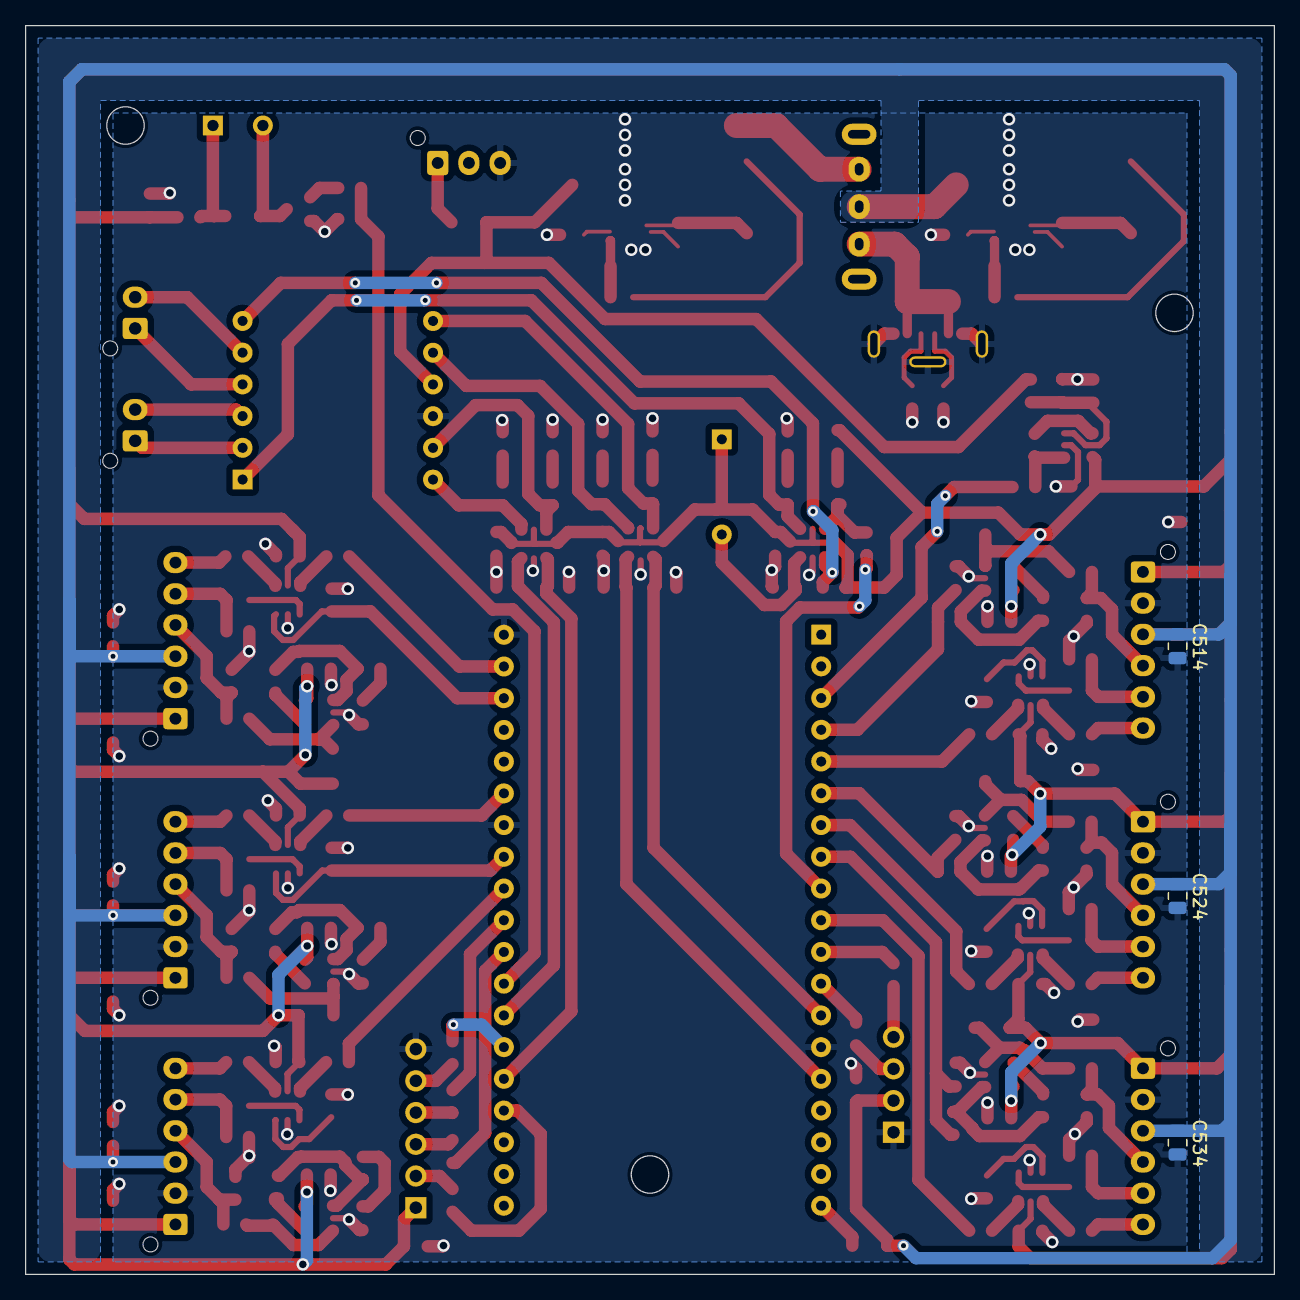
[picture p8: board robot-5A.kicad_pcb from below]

Board: 2 copper layers, 100.0 x 100.0 mm, 193 parts (3 on the bottom side), 135 nets.

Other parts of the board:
D204: LED Jaune; LED_0805_2012Metric
D205: LED Verte; LED_0805_2012Metric

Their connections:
GND: D204.1 (K), D205.1 (K); also elsewhere on the board
unnamed 56: D204.2 (A); also elsewhere on the board
unnamed 57: D205.2 (A); also elsewhere on the board

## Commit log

2023-10-07 Initial commit, ongoing schematic design
    [Pont_H.kicad_sch, Power_Supply.kicad_sch, Sensors.kicad_sch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]
2023-10-08 Make some improvement on shcema mainly on sensor page
    [Pont_H.kicad_sch, Power_Supply.kicad_sch, Sensors.kicad_sch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]
2023-10-11 Fix all ECR warning and error and remove duplicated sensors schema
    [Pont_H.kicad_sch, Power_Supply.kicad_sch, Sensors.kicad_sch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]
2023-10-12 PCB routing with ECR check
    [Pont_H.kicad_sch, Power_Supply.kicad_sch, Sensors.kicad_sch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]
2023-10-12 Add gpio num for DRV8833, buzzer and BattSense
    [robot-5A.kicad_pcb]
2023-10-12 Add gpio num for sensor, LCD and SD (change card size to 100x100mm)
    [robot-5A.kicad_pcb]
2023-10-12 Fix from Guillaume remarks:
    - 200R => 1k For din/dout/adc
    - add capa for buzzer
    - add aop diode protection
    - fix RC sensor adc filter
    [Pont_H.kicad_sch, Power_Supply.kicad_sch, Sensors.kicad_sch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]
2023-10-13 Replace LT8610 by MCP16311 to decrease price (schema only)
    [Power_Supply.kicad_sch, robot-5A.kicad_sch]
2023-10-14 Replace LT8610 by MCP16311 to decrease price (pcb)
    Schema fix fault LED from H-brige
    [Pont_H.kicad_sch, Power_Supply.kicad_sch, robot-5A.kicad_pcb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]
2023-10-15 Remove convert 3.3V choice from 5V or bat and fix from 5V only Remove 3.3V from Esp32 pin header
    [Power_Supply.kicad_sch, robot-5A.kicad_pcb, robot-5A.kicad_sch]
2023-10-16 Add lcsc part number (and change some footprint)
    [Pont_H.kicad_sch, Power_Supply.kicad_sch, Sensors.kicad_sch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]
2023-10-16 Replace 1x02 pin header by DIP switch to enable H-bridge
    [robot-5A.kicad_pcb, robot-5A.kicad_sch]
2023-10-17 Add USB C connector and switch to select 5V from USB-C or 5V DC/DC out
    [Power_Supply.kicad_sch, Sensors.kicad_sch, robot-5A.kicad_pcb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]
2023-10-17 Improve space between composant and track
    [robot-5A.kicad_pcb]
2023-10-17 Add M3 Monting hole
    [robot-5A.kicad_pcb]
2023-10-17 Uniform BOM column and add red dot on all >2 pad components
    [Pont_H.kicad_sch, Power_Supply.kicad_sch, Sensors.kicad_sch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]
2023-10-17 Fix LED fault orientation
    [Pont_H.kicad_sch, Power_Supply.kicad_sch, Sensors.kicad_sch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]
2023-10-17 Update LCSC part number with basic version if exist to decrease price
    [Pont_H.kicad_sch, Power_Supply.kicad_sch, Sensors.kicad_sch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]
2023-10-17 Update TODO when remove 1x02 pin header by DIP switch
    [robot-5A.kicad_sch]
2023-10-17 Update PCB
    [robot-5A.kicad_pcb]
2023-10-17 Add script to generate BOM and pos in JLCPCB format
2023-10-17 Fix some component name
    [robot-5A.kicad_pcb, robot-5A.kicad_sch]
2023-10-17 Some design review remarks added
    [Power_Supply.kicad_sch, Sensors.kicad_sch, robot-5A.kicad_sch]
2023-10-17 Add pin header female for ESP32, DRV8833 and SD card
    [Pont_H.kicad_sch, lcd_sd.kicad_sch, robot-5A.kicad_sch]
2023-10-17 taken into account power supply remarks
    [Power_Supply.kicad_sch, robot-5A.kicad_pcb, robot-5A.kicad_sch]
2023-10-17 taken into account sensors remarks
    [Sensors.kicad_sch, robot-5A.kicad_pcb]
2023-10-17 taken into account USB-C remark
    [robot-5A.kicad_pcb, robot-5A.kicad_sch]
2023-10-17 taken into account bat sense remark
    [Power_Supply.kicad_sch, robot-5A.kicad_pcb, robot-5A.kicad_sch]
2023-10-17 taken into account power switch remark
    [robot-5A.kicad_pcb, robot-5A.kicad_sch]
2023-10-18 Split DVR8833_EVM into IN and OUT to be able to have a pin header for each
    [Pont_H.kicad_sch, robot-5A.kicad_pcb, robot-5A.kicad_sch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]
2023-10-18 Split ESP32-DevKicC into Left and Right to be able to have a pin header for each
    [robot-5A.kicad_pcb, robot-5A.kicad_sch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]
2023-10-18 Do not include JST XH in BOM and change option to generate Gerber and Drill files
    [Sensors.kicad_sch, lcd_sd.kicad_sch, robot-5A.kicad_pcb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]
2023-10-18 Increase some hole from JLCPCB 3d preview and fix USB-C position
    [robot-5A.kicad_pcb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]
2023-10-26 Remove dependency on shared lib
    [Pont_H.kicad_sch, Power_Supply.kicad_sch, Sensors.kicad_sch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]
2024-12-27 Fix inverted battsense Op Amp, remove adc in clamp diode, invert din and dout silkscreen
    [Sensors.kicad_sch, robot-5A.kicad_pcb, robot-5A.kicad_sch]
2025-01-06 Update for kikad 8 and use new script to generate pos
    [Pont_H.kicad_sch, Power_Supply.kicad_sch, Sensors.kicad_sch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]
2025-04-24 Some BOM and gerber export fix and improvement
